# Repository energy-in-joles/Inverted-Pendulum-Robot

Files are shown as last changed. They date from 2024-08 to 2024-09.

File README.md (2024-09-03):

# Inverted-Pendulum-Robot (Furuta Pendulum)

<p align="center">
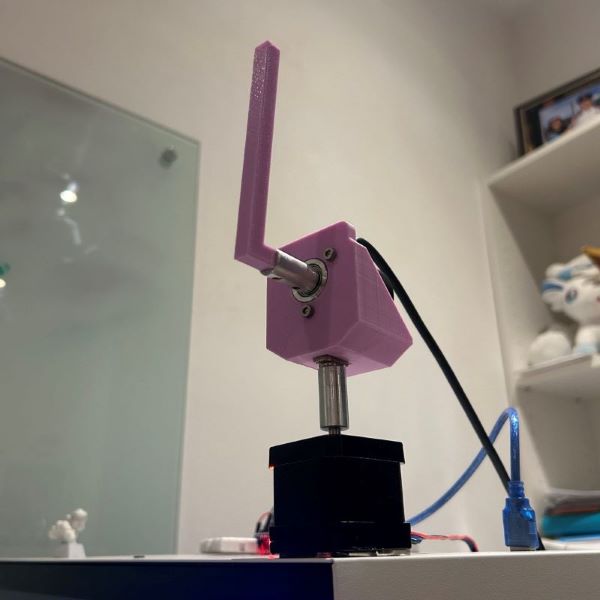
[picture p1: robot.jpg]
  
</p>

## Introduction

A Furuta Pendulum is a control problem which involves a driven arm (free-rotating in the vertical plane) attached to a horizontal rotating plane. The goal of the robot is to balance the arm in the vertical position. This is a more advanced adaptation of the classic [cartpole problem](https://gymnasium.farama.org/environments/classic_control/cart_pole/), where it includes swing-up (swinging the arm to the vertical position in the first place).

## Hardware Implementation

The following parts were procured for the robot assembly:
1. [Nema 17 Stepper Motor 2.8V](https://thepihut.com/products/nema-17-stepper-motor-42mm-x-40mm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)
2. [600 PPR Photoeletric Incremental Rotary Encoder](https://www.aliexpress.com/item/1005005071771659.html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)
3. [Motor Driver Board](https://www.aliexpress.com/item/1005003166428228.html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)
4. [12V 2A Power Supply Plug Charger](https://www.lazada.sg/products/msrc-safety-5v-12v-1a-2a-3a-100-240v-mains-transformer-acdc-adapter-uk-plug-charger-power-supply-i1875876088-s10002441740.html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)
5. DRV8825 Stepper Motor Driver
6. Arduino Nano

The pendulum and encoder housing were designed in Fusion 360 and produced with FDM printing. The `.step` and `.f3d` files can be found in `/robot/CAD`.

The pendulum was attached to the encoder with a rigid shaft coupler. The encoder housing was attached to the stepper motor with a modified M6 bolt in a T-nut fitted in another rigid shafter coupler.

The Arduino communicates with the Python script with bi-directional serial communication, where it:
1. Reads the acceleration input for the motor from the PC and implements it.
2. Writes the motor position and pendulum position data for generating the observation space for the model.
3. Implements reset functions for resetting the motor position and encoder value.

## Pendulum Env ##

Follows the standard Gymnasium class format. Defined below is the observation space, action space, and reward function used for the experiment:

- $\theta$: angular position of pendulum. 0 at the top and normalised between $[-\pi,\pi]$.
- $\dot{\theta}$: angular velocity of pendulum. Experimentally bounded between $[-10,10]$, then normalised to between $[-2, 2]$.
- $\alpha$: motor position (measured in steps instead of angle). Steps range physically limited to 90&deg; left and right or $[-200, 200]$ step range. However, observation space spans further between $[-300, 300]$ to account for the motor exceeding the limit slightly. The range is then normalised between $[-3,3]$.
- $\dot{\alpha}$: motor velocity (steps per second). Experimentally bounded between $[-4, 4]$, then normalised to between $[-1, 1]$
- $\ddot{\alpha}$: motor acceleration (steps per second squared). Control input into the system. Bounded between $[-20000,20000]$ and normalised between $[-2, 2]$.

Note that all values are continuous.

### Observation Space ###
$\left[\cos{\theta}, \sin{\theta}, \dot{\theta}, \alpha, \dot{\alpha}\right]$

`ndarray` of size (5,) containing 5 continuous observation values. Using $\cos$ and $\sin$ values of $\theta$ experimentally showed better convergence rates than just $\theta$.

### Action Space ###
$\left[\ddot{\alpha}\right]$

`ndarray` of size (1,) containing motor acceleration value. Continuous action space.

### Reward Function ###
$\gamma-\left(\theta^2+C_1\times\dot{\theta}^2+C_2\times\alpha^2+C_3\times\dot{\alpha}^2+C_4\times\ddot{\alpha}^2\right)$

$\gamma$: reward offset value (offset) to ensure that reward is always positive. 

If reward was $-\inf$ to $0$, episodes with early termination would generate a higher reward (because they would accumulate smaller negative reward), resulting in a faulty reward system. Hence, the offset aims to prevent this issue. Constants $C$ are used to adjust the reward function weightage and are defined in the `/conf/config.yaml`.

### Termination
The environment terminates when the stepper motor exceeds the allowed range of motion (more than 90&deg; left or right from the zero position).

### Truncation
The environment is truncated after 500 timesteps, but this can be adjusted in `/conf/mode/train.yaml`.

## Usage

### Configuration

The script provides a high level of flexibility for training and evaluating the model. Configurations are stored in the `conf` folder, organised in the following manner:
1. `config.yaml`
    - model selection (PPO or SAC)
    - mode selection (train or eval)
    - serial communication configuration between PC and arduino
    - action and observation space configuration
    - reward function weights
    - toggle logging with tensorboard
2. `/mode/train.yaml`:
    - new model file configuration 
    - device config (cuda or cpu)
    - training total timesteps and episode length
3. `/mode/eval.yaml`:
    - device config (cuda or cpu)
    - episode length set to -1 for infinite episode length
4. `/model` (`PPO.yaml` and  `SAC.yaml`) config files:
    - model weights

### Install and Run

1. To run the code, first build dependencies in the root directory with:
```pip install -e .```

2. Upload the Arduino code in `/robot/arduino/main/main.ino` to the Arduino board.

3. Connect the robot to the PC and run the script, remembering to set the mode to `train`:
```python src/main.py```

4. The trained model will then be stored in `/model`, where it can be trained further or evaluated.

## Credits
We largely referred to the following resources for guidance:
1. Armandpl's [video](https://www.youtube.com/watch?v=Y6FVBbqjR40) and [repository](https://github.com/Armandpl/furuta/tree/master?tab=readme-ov-file#mlops) on building a similar project as us.
2. Inspiration for this project was taken from Quanser Qube design. Reward function adapted from Quanser's [code](https://git.ias.informatik.tu-darmstadt.de/quanser/clients/-/tree/master/quanser_robots/qube).
3. Stable Baseline's [guide](https://stable-baselines.readthedocs.io/en/master/guide/custom_env.html) on custom environment creation.
4. [Farama's guide on handling termination vs truncated scenarios](https://gymnasium.farama.org/tutorials/gymnasium_basics/handling_time_limits/) when designing our environment.

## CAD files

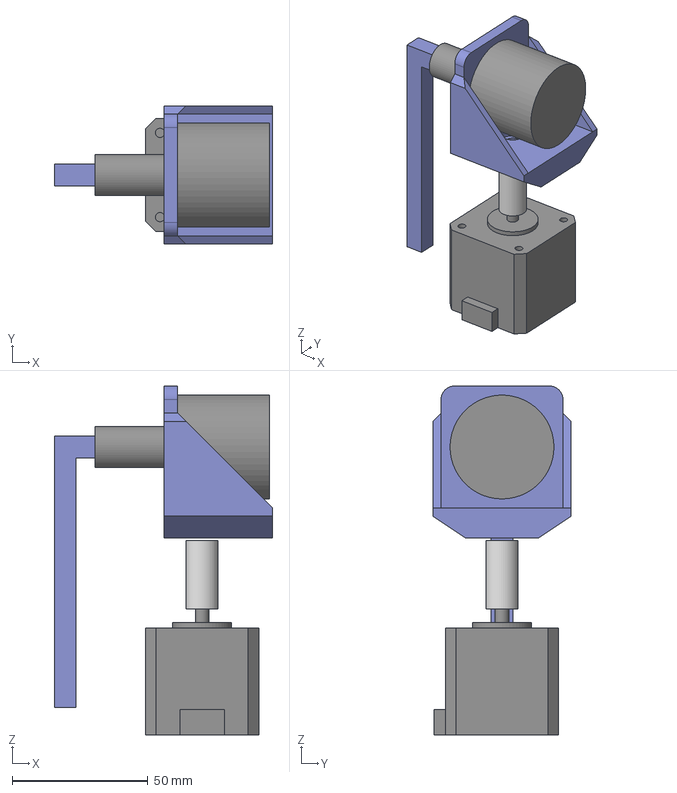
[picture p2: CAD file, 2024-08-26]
robot/CAD/inverted_pendulum_robot_assy.step
80.5 x 51.0 x 128.7 mm
Stepper Motor
Rotary Encoder
Motor Coupler
Pendulum
Encoder Housing x 2

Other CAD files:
robot/CAD/inverted_pendulum_robot_assy.f3d

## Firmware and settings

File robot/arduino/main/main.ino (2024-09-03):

#include <Encoder.h>
#include <FlexyStepper.h>

const int ENCODER_PIN_A = 2;
const int ENCODER_PIN_B = 3;
const int MOTOR_STEP_PIN = 4;
const int MOTOR_DIR_PIN = 7;
const int MOTOR_EN_PIN = 8;
const int MOTOR_STEP_LIMIT = 200; // 90 DEG limit (800 steps per rev for quarter step setting: 90 DEG == 200 steps)
const int TARGET_POS = 10000; // a large value that the motor will never reach (sets direction for motor spin)
const int MAX_SPEED = 1000;

const int BAUDRATE = 31250;
const String AUTH_STR = "<ready>"; // matching auth string in python script
const int RESET_CMD = 32767;
const int RESET_ENCODER_CMD = 32766;

byte inputBuffer[sizeof(int)];
byte outputBuffer[4];

FlexyStepper stepper;
Encoder myEnc(ENCODER_PIN_A, ENCODER_PIN_B);

// read serial data from python script: 2 byte signed acceleration value
int read_serial() {
  int accel_in = 0;
  size_t num_read = Serial.readBytes(inputBuffer, sizeof(int));
  if (num_read == sizeof(int)) {
    accel_in = *((int*) inputBuffer);
  }
  return accel_in;
}

// prepare output buffer to send position and loop index data to python script
// buffer: 22 bits for encoder position (little endian), 10 bits for stepper pos
void update_output_buffer(byte *outputBuffer, long encoderPos, int currentStepperPos) {
  outputBuffer[0] = (encoderPos >> 0) & 0xFF;
  outputBuffer[1] = (encoderPos >> 8) & 0xFF;
  outputBuffer[2] = (encoderPos >> 14) & 0xFC | (currentStepperPos >> 8) & 0x03;
  outputBuffer[3] = (currentStepperPos >> 0) &0xFF;
}

void reset_pos() {
  stepper.setAccelerationInStepsPerSecondPerSecond(20000);
  stepper.moveToPositionInSteps(0);
}

void setup() {
  Serial.begin(BAUDRATE);
  pinMode(MOTOR_EN_PIN, OUTPUT);
  digitalWrite(MOTOR_EN_PIN, LOW);

  // connect and configure the stepper motor to its IO pins
  stepper.connectToPins(MOTOR_STEP_PIN, MOTOR_DIR_PIN);
  stepper.setCurrentPositionInSteps(0);
  stepper.setSpeedInStepsPerSecond(MAX_SPEED);
  delay(10);
  Serial.println(AUTH_STR);
}

int accel_in = 0;
bool isResting = true; // prevent motor from running at start without any input
bool isGoingRight = false;
int currentStepperPos = 0;

void loop() {
  if (Serial.available() > 0) {
    accel_in = read_serial();
    // reset stepper back to start position
    if (accel_in == RESET_CMD) {
      reset_pos();
      isResting = true;
      accel_in = 0;
      Serial.println(AUTH_STR);
      return;
    } 
    // reset encoder value when close to overflow
    if (accel_in == RESET_ENCODER_CMD) {
      isResting = true;
      accel_in = 0;
      myEnc.write(0);
      return;
    }

    long newPosition = myEnc.read();
    // update python script with positional information
    update_output_buffer(outputBuffer, newPosition, currentStepperPos);
    for (int i = 0; i < sizeof(outputBuffer); i++) {
      Serial.write(outputBuffer[i]);
    }
  }

  // move motor and update motor movement information
  if (abs(accel_in) > 0) {
    isResting = false;
  }

  if (accel_in < 0 || accel_in == 0 && !isGoingRight) {
    stepper.setTargetPositionInSteps(-TARGET_POS);
    isGoingRight = false;
  }
  else {
    stepper.setTargetPositionInSteps(TARGET_POS);
    isGoingRight = true;
  }
  // update motor movement using accel_in value
  stepper.setAccelerationInStepsPerSecondPerSecond(abs(accel_in));

  currentStepperPos = stepper.getCurrentPositionInSteps();
  if (currentStepperPos <= MOTOR_STEP_LIMIT && currentStepperPos >= -MOTOR_STEP_LIMIT && !isResting) {
    stepper.processMovement();
  }
}

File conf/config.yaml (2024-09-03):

defaults:
  - _self_
  - mode: train
  - model: SAC
  - override hydra/hydra_logging: disabled
  - override hydra/job_logging: disabled

model_filename: "model_100_4"
model_dir_name: "model"
control_frequency: 55 #55 Hz

# only relevant for train_model_with_tensorboard
logging:
  enabled: False
  dir_name: "logs" # for logging training progress data
  run_name: "model_100_4"

serial:
  in_buffer_size: 4
  out_buffer_size: 2
  baudrate: 31250
  port: 'COM3'
  timeout: 1
  max_startup_t: 5
  auth_str: "<ready>"
  sleep_t: 0.01

encoder:
  reset_encoder_t: 20
  encoder_reset_thresh: 600 # number of rotations in encoder before resetting encoder
  # if rotations in one direction is too large and not reset, the encoder data will overflow.

action_space:
  actual_half_range: 20000
  half_range: 2

# element position: cos theta, sin theta, angular_vel, motor_pos, motor_vel
observation_space:
  lower_bound: [-1, -1, -10, -3, -4]
  upper_bound: [1, 1, 10, 3, 4]

# motor half_range can record up to 300, but is bounded to 200
calc:
  vel_modifier: 0.2
  motor_vel_modifier: 0.25
  motor_half_range: 300
  motor_half_limit: 200
  motor_norm_half_range: 3

reward:
  vel_weight: 0.1
  motor_pos_weight: 0.2
  motor_vel_weight: 0.02
  control_weight: 0.2
  reward_offset: 15
  # old control: 0.1, old motor_pos_weight: 0.05, vel_weight: 0.05

hydra:
  output_subdir: null
  run:
    dir: .

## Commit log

2024-07-21 added basic motor_test/read_sensor files
2024-07-28 implemented angular position, velocity and acceleration calculation
2024-07-28 implemented motor control and motor angle limit
2024-07-28 added code to correctly handle 0 acceleration
    [main.ino]
2024-08-01 added motor position to telemetry data
2024-08-01 added reset command stub
    [main.ino, pendulum_env.py]
2024-08-03 fully implemented step and reset function in pendulum env
    [config.yaml, main.ino, motor_test_flexy.ino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]
2024-08-04 replaced incorrectly used truncated with terminated in rwd function
    [pendulum_env.py]
2024-08-11 [MILESTONE] semi-optimal implementation: increased baud rate, implemented encoder reset and tweaked params.
    [config.yaml, main.ino, pendulum_env.py]
2024-08-26 some file restructuring
    [inverted_pendulum_robot_assy.f3d, inverted_pendulum_robot_assy.step]
2024-08-28 added keyboard interrupt for eval function
2024-08-28 added device config
2024-09-03 shifted position calculation to be handled by env. Implemented keyboard interrupt for training
2024-09-03 fixed error in bit shifting; corrected some code comments and error messages
    [config.yaml, main.ino, pendulum_env.py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]
2024-09-03 removed redundant print function and fixed overwrite config implementation
    [util.py]
